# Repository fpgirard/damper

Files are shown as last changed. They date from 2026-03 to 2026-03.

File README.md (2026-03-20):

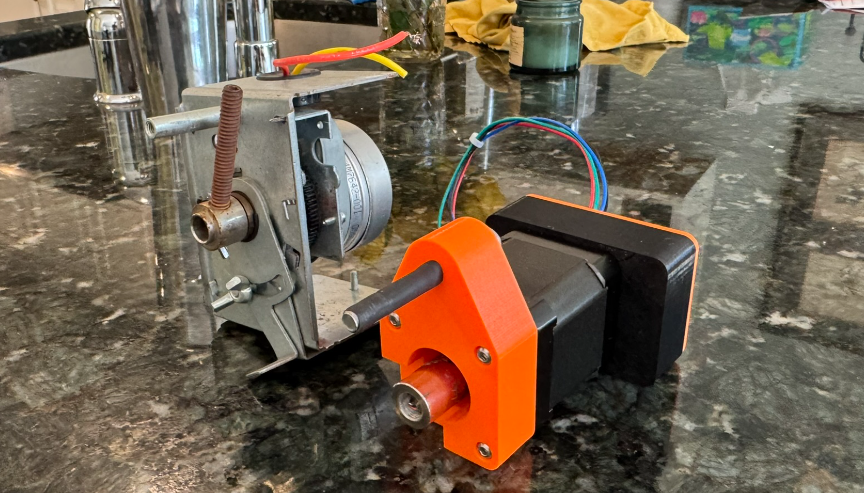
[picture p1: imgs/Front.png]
# A PID-based Damper To Replace Honeywell Damper Motors

## Components

The solution has the following hardware and software components:

* [VAL3000 Controller](https://github.com/Valar-Systems/VAL3000)  
* A [STEPPERONLINE NEMA-17 Motor](https://www.amazon.com/dp/B00PNEQKC0)  
* 3D Printed Mount and PCB case  
* An [8mm-\>5mm collar](https://a.co/d/04N5h7Px)  
* Two (2) M3 x 50mm pan head bolts to mount PCB case  
* Four (4) M3 x 20 hex bolts to mount the bracket  
* One (1) M4 x 20 hex bolt as a StallGuard stop  
* [Simple PID integration from HACS](https://github.com/bvweerd/simple_pid_controller)  
* Home Assistant with yaml file for ESPhome & automations

## Rationale & Approach

Heat and AC on our 2nd floor is poorly distributed.  A single large vent that feeds 4 outlets in our master bedroom and bath represents about 50% of the floor’s airflow while the remaining 50% feeds 3 bedrooms and 2 baths via a series of 12 inch flex vents.  Insufficient air flow feeds these guest rooms.

Some attic exploring discovered a non-functioning damper on the master bedroom duct so we proceeded with replacing the defunct Honeywell M847D1012 & M847D-ZONE motor with a positioning stepper motor. Combining this stepper with an ESPHome device, and a simple PID controller, we hoped for a chance to level the heating/cooling field.

For starters, a few assumptions:

1. We will configure ESPHome using HA’s cover and number templates.  HA’s ‘cover’ lets us fully open, stop, and close the damper.   HA’s ‘number’ allows us to set the damper to any opening level.  Dampers are a 90 degree device.  Since we’re using 8 microsteps on a 200 step/revolution motor, a full rotation is 1600 so 90 degrees is 400 steps.   Leaving 20 steps as margin, our damper has an “OPEN” value of 20 steps and “CLOSED” is 380\.  We also used Trinamic’s StallGuard technology.  I recommend you stick with the StallGuard parameters provided.  
2. For this stack, we set:  
   a. The input as the difference between the master bedroom thermostat (T1) and one of the guest bedrooms (T2). T1 \- T2 (aka ‘error’)
   b. Delta sensor — mode-aware, reverses math for heat/cool, returns 0 when off
   c. PID controller — kp: -36.0 ki: -0.5 kd: -5.0, setpoint 0 
   d. Position accumulator — input_number.damper_position min:20 max:380 initial:20
   e. Stepper action — absolute PID output, clamped and sent to both accumulator and stepper
   f. Negative gains provide inverted PID convention in hass-pid-controller

3. There's also an automate that turns on/off the PID controller if the thermostat (via climate entity) is off and on otherwise.

View the README files in the individual sub-directories for greater detail on this implementation.  You might have to tune the Kp, Ki, & Kd gains to match your installation.

## Components

### Hardware 

I like the STEPPERONLINE motor.   For \~$15, it’s powerful and reliable.   Valar System’s VAL3000 is a robust, elegant ESP32 PCB integrated with a Trinamic 2209 controller.  This board made this project easy and I highly recommend it.  I decreased the current by 50% by setting the irun value for the TMC220 to 15.

3D printed cases are OpenSCAD designs.  STL files are also provided.  See above bolts to attach them.

### Software

Home Assistant is required and you will need to create and modify 4 home assistant files:

* A ESPhome Builder <span style="font-family:Courier">damper.yaml</span> configuration file  
* If you want to fiddle with the StallGuard4 parameters, use the ESPhome Builder testing <span style="font-family:Courier">get-tstep.yaml</span> file to obtain the TSTEP values of your damper controller.  
* An automation, <span style="font-family:Courier">pid2controller.yaml</span> to write the PID output to the control\_stepper number.  This is a bit tricky as I’ve learned because the PID output state doesn’t change if the value remains the same so it’s timer \- not state-based.  
* An automation, <span style="font-family:Courier">handleClimate.yaml</span> to enable or disable the PID controller based on the thermostat setting (heat or off).  The simple PID integration I used has an Auto-Mode\!

## Reference Materials

This is a hodge podge of sites that I used to understand the various aspects of this project.  Shout out to [Daniel](https://github.com/daniel-frenkel/Valar-Systems) at Valar Systems and [Christian](https://github.com/slimcdk) for his ESPHome contributions.  Daniel’s book on working with stepper motors was a huge help \- get a copy of it if you can\!

### API between ESPhome and HA:

[https://esphome.io/components/api/\#:\~:text=After%20adding%20an%20api:%20line,will%20only%20refer%20to%20Actions](https://esphome.io/components/api/#:~:text=After%20adding%20an%20api:%20line,will%20only%20refer%20to%20Actions).  
[https://esphome.io/components/stepper/](https://esphome.io/components/stepper/)  
[TMC2009 & ESPHome](https://github.com/slimcdk/esphome-custom-components/tree/11b380a829b23ce5282488113e5af97a6d5236ad/esphome/components/tmc2209)

### UART wiring

[https://forum.arduino.cc/t/tmc2209-and-esp32-uart-wiring/1362812/17](https://forum.arduino.cc/t/tmc2209-and-esp32-uart-wiring/1362812/17)  
[https://github.com/bigtreetech/BIGTREETECH-TMC2209-V1.2/blob/master/manual/TMC2209-V1.2-manual.pdf](https://github.com/bigtreetech/BIGTREETECH-TMC2209-V1.2/blob/master/manual/TMC2209-V1.2-manual.pdf)

### Community Contributions

[Having motor go to position based on input box](https://community.home-assistant.io/t/is-it-possible-to-control-a-stepper-through-a-box-input-number/476943).  
[https://www.reddit.com/r/homeassistant/comments/1qreal5/comment/o2p8kz4/](https://www.reddit.com/r/homeassistant/comments/1qreal5/comment/o2p8kz4/)  
[Stepper Component \- ESPHome \- Smart Home Made Simple](https://esphome.io/components/stepper/#home-assistant-configuration)  
[ESP32 Wi-Fi Stepper Motor Driver : r/diyelectronics](https://www.reddit.com/r/diyelectronics/comments/1p7i9f4/esp32_wifi_stepper_motor_driver/)  
[https://valarsystems.com/products/val3000](https://valarsystems.com/products/val3000) & [https://www.youtube.com/shorts/FnWmoFnG2Ak](https://www.youtube.com/shorts/FnWmoFnG2Ak)  
[https://community.home-assistant.io/t/motorized-inline-hvac-damper-for-zone-control/872555](https://community.home-assistant.io/t/motorized-inline-hvac-damper-for-zone-control/872555)  
[Arduino & TMC & UART woes](https://forum.arduino.cc/t/using-a-tmc2209-silent-stepper-motor-driver-with-an-arduino/666992/10)

[https://www.reddit.com/r/Esphome/comments/1qxsh61/got\_my\_stepper\_driver\_integrated\_with\_esphome/](https://www.reddit.com/r/Esphome/comments/1qxsh61/got_my_stepper_driver_integrated_with_esphome/)  
TMC2209 Support  
[https://github.com/slimcdk/esphome-custom-components/tree/master/esphome/components/tmc2209](https://github.com/slimcdk/esphome-custom-components/tree/master/esphome/components/tmc2209)  
[https://valarsystems.com/products/val3000](https://valarsystems.com/products/val3000)

### Basic homing in esphome:

[https://www.reddit.com/r/homeassistant/comments/1qxt8o1/thanks\_guys\_my\_stepper\_driver\_now\_works\_with/](https://www.reddit.com/r/homeassistant/comments/1qxt8o1/thanks_guys_my_stepper_driver_now_works_with/)  
[https://www.reddit.com/user/nutstobutts/](https://www.reddit.com/user/nutstobutts/)  
[https://www.reddit.com/user/c7ndk/](https://www.reddit.com/user/c7ndk/)  
[https://www.reddit.com/r/homeassistant/comments/1qreal5/comment/o38b9ty/?context=3](https://www.reddit.com/r/homeassistant/comments/1qreal5/comment/o38b9ty/?context=3)  
[https://www.reddit.com/r/homeassistant/comments/1qreal5/comment/o38b9ty/?context=3](https://www.reddit.com/r/homeassistant/comments/1qreal5/comment/o38b9ty/?context=3)  
[https://github.com/slimcdk/esphome-custom-components/blob/master/esphome/components/tmc2209/README.md\#sensorless-homing](https://github.com/slimcdk/esphome-custom-components/blob/master/esphome/components/tmc2209/README.md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)  
[https://github.com/AndreaFavero71/stepper\_sensorless\_homing](https://github.com/AndreaFavero71/stepper_sensorless_homing)

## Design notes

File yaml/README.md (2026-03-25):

# YAML Files Required for Damper Control

These files use entity, device, and automation names that are unique for my home.  You will need to replace them with your corresponding values.
They are:

damper.yaml - the ESPHome configuration file for the VAL3000
get-tstep.yaml - a test ESPHOME configuration file that will provide you with an accurate TSTEP value
handleClimate.yaml - sets the damper to the ideal position given difference presence scenarios (see below)
input_number.yaml - a helper to persistently store the damper position
template.yaml - the delta temperature between the 2 zones.

There are 8 different presence scenarios across the 3 rooms:

| Bedroom | Office | Guest Room | Damper Position |
|---|---|---|---|
| Vacant | Vacant | Vacant | Open |
| Vacant | Vacant | Occupied | Closed |
| Vacant | Occupied | Vacant | Closed |
| Vacant | Occupied | Occupied | Closed |
| Occupied | Vacant | Vacant | Open |
| Occupied | Vacant | Occupied | PID |
| Occupied | Occupied | Vacant | PID |
| Occupied | Occupied | Occupied | PID |

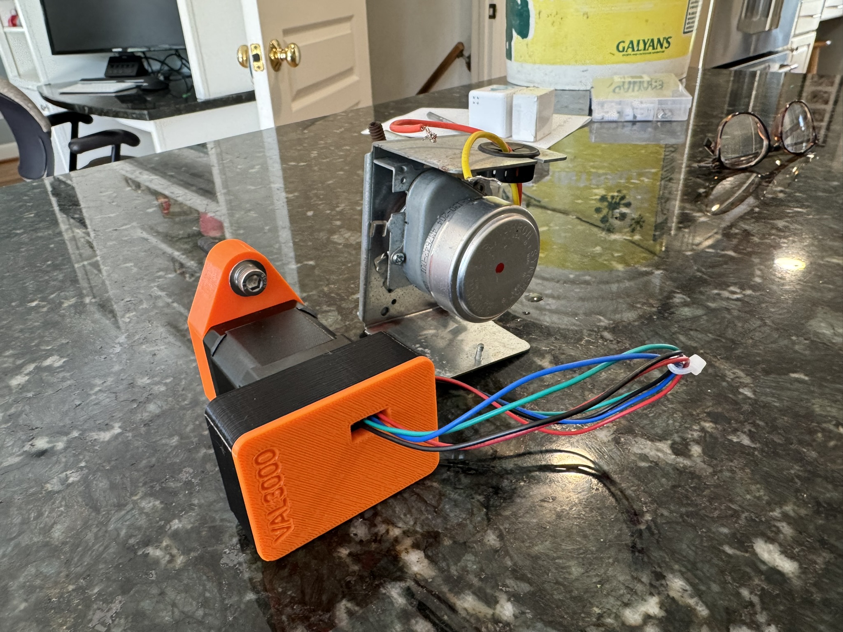
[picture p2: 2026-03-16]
imgs/Back.JPEG

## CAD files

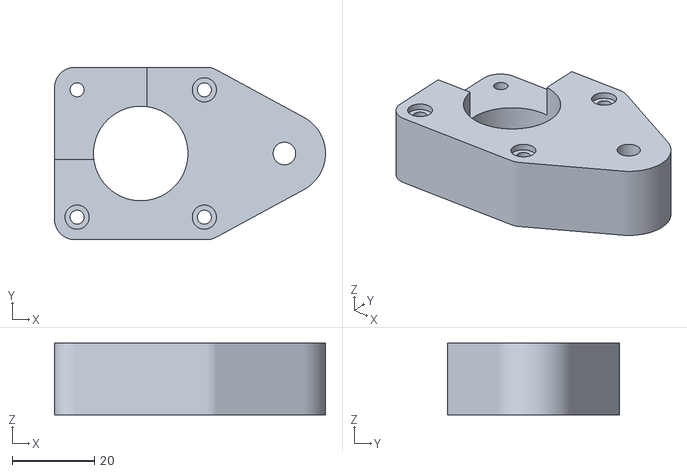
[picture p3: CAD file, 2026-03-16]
stl/damper.stl
66.0 x 42.0 x 17.5

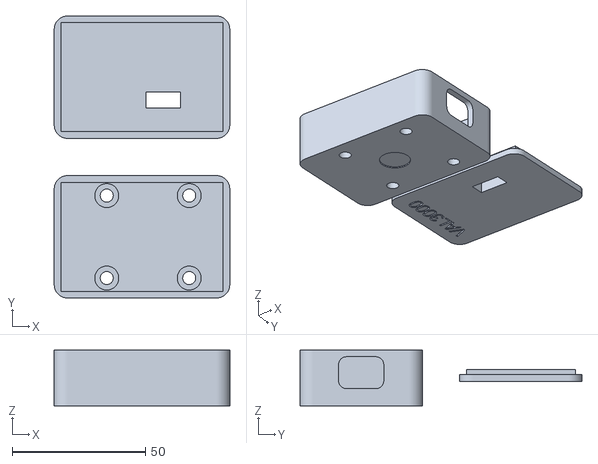
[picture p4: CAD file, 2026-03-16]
stl/damper-case.stl
66.0 x 106.0 x 21.0

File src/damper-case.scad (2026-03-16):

include <BOSL2/std.scad>
$fn=128;

// Mount offset
w  = 61; l = 41; h = 16;    // x,y,z
usb_w = 12; usb_l = 17; usb_h = 12;
hole_w = 31; hole_l = 31;
wire_w = 14; wire_l = 10; wire_h = 6;
wall = 2.5;
post_d = 9; post_h = 6;
mag_d = 12.5; mag_h = 3;
floor = 3;

module mirror2(v) {
    children();
    mirror(v) children();
}
module base() { 
   difference() { 
       union() {
           difference() {
               cuboid([w+2*wall,l+2*wall,h+2*wall], rounding=5, edges="Z"); 
               translate([0,0,floor]) cuboid([w,l,h+6]);  } // main cabin}
           translate([7.5/2-1.5,0,.5]) { //posts
              for ( i = [-1,1] ) {    // Feet
                 for (j=[-1,1]) {
                    translate([i*(hole_w)/2,j*(hole_l)/2,-11]) {
                        cylinder(post_h,d=post_d);
                    }    
                  }
              }
           }
       }        
       translate([w/2,0,2]) rotate([0,90,0])cuboid([usb_w,usb_l,usb_h],rounding=3);   // power connectors
       //translate([5,l/2,-1]) cuboid([wire_w,wire_l,wire_h],rounding=2);   // motor wires!
       translate([0,0,-13]) cylinder(mag_h,d=mag_d);   // magnet
       translate([7.5/2-1.5,0,1.5]) {
         for ( i = [-1,1] ) {    // holes that penetrate box and posts
            for (j=[-1,1]) {
              translate([i*(hole_w)/2,j*(hole_l)/2,-14]) {
                  cylinder(post_h+3,d=4.9);
                    
              }
            }
         }
       }
    }
}
module cap() {
  difference() {
      union() {
        cuboid([w+2*wall,l+2*wall, wall], rounding=5, edges="Z"); 
        translate([0,0,2]) cuboid([w,l,wall]); // main cabin}
      }
      translate([w/2-22.5,-l/2+12,0]) cuboid([13,6,22]);
      translate([-25,0,-wall+1]) {
        linear_extrude(1) {
          rotate([0,0,90]) mirror([1,0,0]) text("VAL3000", size=6, valign="center", halign="center",direction="ltr");}}
    
  }
}
translate([0,60,0]) cap();
base();

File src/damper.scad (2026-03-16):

include <BOSL2/std.scad>
include <BOSL2/screws.scad>
$fn=128;
// Aqara T1 Shutoff Valve
frame = 42;
span = 31;
thick = 17.5;
shank = 23;
post = 35;

module mirror2(v) {
    children();
    mirror(v) children();
}
module base() {
  difference() {
     hull() { 
         cuboid ([frame,frame,thick], rounding=5, edges="Z"); 
         translate([post,0,0]) cylinder(thick,d=20, center=true);
     } // frame
     cylinder(d=shank,h=thick,center=true); // cutout for shaft shank
     mirror2([0,1,0]) mirror2 ([1,0,0]) translate([span/2,span/2,0]) screw_hole("M3,17.5",head="socket",counterbore=3); // mount holes
     translate([post,0,0]) screw_hole("M5", length=thick);
     translate([-frame/2+3/2,frame/2-3/2,10]) cuboid ([frame,frame,thick], rounding=5, edges="Z");
     }
}
base();  // mount

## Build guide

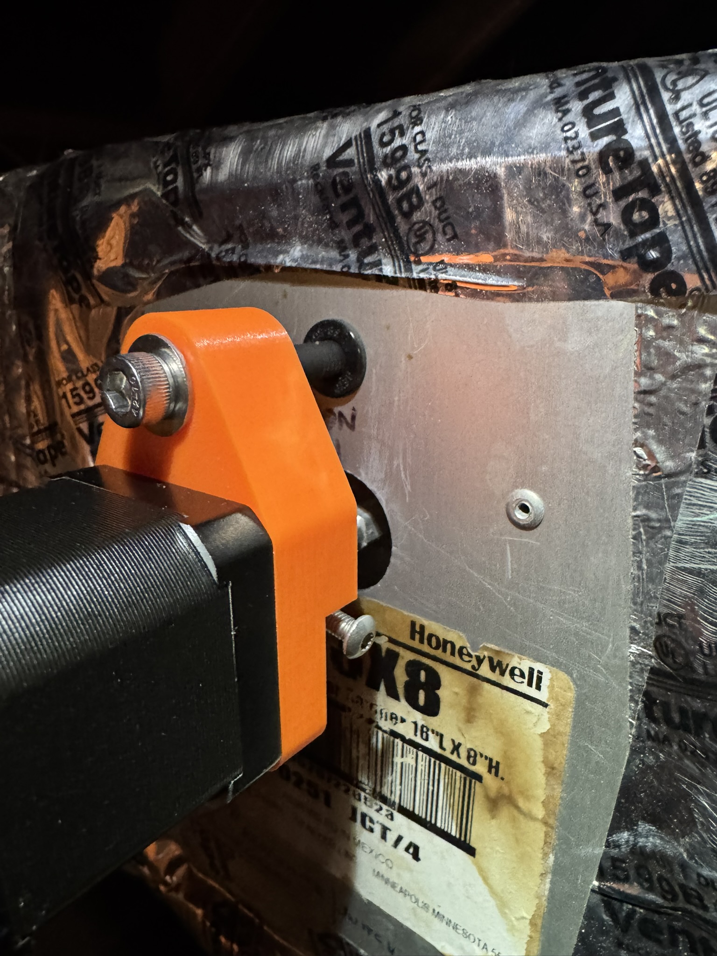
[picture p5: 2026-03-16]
imgs/Installed.JPEG

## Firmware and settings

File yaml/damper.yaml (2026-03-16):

# 
external_components:
  - source: github://slimcdk/esphome-custom-components
    components: [tmc2209_hub, tmc2209, stepper]

substitutions:
  stepper_direction: "cw" # change to "cw" or "ccw" to change direction
  max_distance_steps: 380 # 10 steps from a full 90 degrees
  min_distance_steps: 20  # 0 steps from home

api:

ota:
  - platform: esphome

logger:

esp32:
  board: esp32-c3-devkitm-1
  framework:
    type: esp-idf

wifi:
  ssid: !secret wifi_ssid
  password: !secret wifi_password

web_server:
  port: 80

esphome:
  name: damper
  on_boot:
    - tmc2209.configure:
        direction: cw
        microsteps: 8
        interpolation: true
        tcool_threshold: 600
        tpwm_threshold: 150
    - tmc2209.stallguard:
        threshold: 55
    - tmc2209.currents:
        standstill_mode: normal
        irun: 15 # 0-31. 31 = 2A current
        ihold: 0
        tpowerdown: 0
        iholddelay: 0
    - button.press: home # home right after boot

globals:
  - id: has_homed
    type: bool
    initial_value: "true"
    restore_value: no

uart:
  tx_pin: 6
  rx_pin: 5
  baud_rate: 500000

stepper:
  - platform: tmc2209
    id: driver
    max_speed: 2000 steps/s # Faster speed is louder
    acceleration: 2000 steps/s^2
    deceleration: 2000 steps/s^2
    config_dump_include_registers: true
    rsense: 100 mOhm
    vsense: False
    enn_pin: 8
    index_pin: 0
    diag_pin: 1
    on_stall:
      - logger.log: "Motor stalled!"
      - stepper.stop: driver
      - if:
          condition:
            lambda: return !id(has_homed);
          then:
            - stepper.report_position:
                id: driver
                position: 0
            - stepper.set_target:
                id: driver
                target: ${min_distance_steps}
            - globals.set:
                id: has_homed
                value: "true"
            - logger.log: "Home position set"

cover:
  - platform: template
    id: damper_cover
    device_class: damper
    has_position: true
    assumed_state: false
    lambda: "return 1.0 - (id(driver)->current_position / ${max_distance_steps});"
    name: Damper
    stop_action:
      - stepper.stop: driver
    close_action:
      - stepper.set_target:
          id: driver
          target: !lambda return ${max_distance_steps} ;
    open_action:
      - stepper.set_target:
          id: driver
          target: !lambda return ${min_distance_steps} ;

button:
  - platform: template
    name: Home
    id: home
    on_press:
      - logger.log: "Going home!"
      - globals.set:
          id: has_homed
          value: "false"
      - stepper.set_target:
          id: driver
          target: -200000

sensor:
  - platform: template
    name: "Position"
    id: my_position
    unit_of_measurement: steps
    lambda: return id(driver).current_position;
    update_interval: 1s

number:
  - platform: template
    name: Stepper Control
    id: stepper_control
    min_value: ${min_distance_steps}
    max_value: ${max_distance_steps}
    optimistic: true
    step: 1
    set_action:
      then:
        - stepper.set_target:
            id: driver
            target: !lambda 'return x;'
